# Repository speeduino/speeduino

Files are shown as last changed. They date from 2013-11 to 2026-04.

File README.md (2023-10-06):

<div align="center">

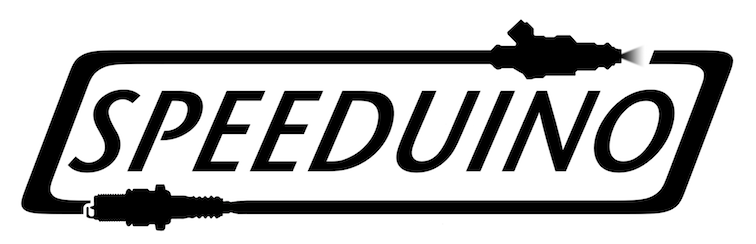
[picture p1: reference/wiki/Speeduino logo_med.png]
Speeduino











##### A low cost, DIY friendly Engine Management System (ECU) based on the Arduino framework
</div>

## Speeduino
The Speeduino project is a flexible, fully featured Engine Management Systems (EMS aka ECU) based on the low cost and open source Arduino platform. It provides the hardware, firmware and software components that make up an engine management system, all provided under open licenses. With over 1000 installations, Speeduino has matured into a product that meets the needs of the hobbyist and enthusiast community without driving prices to the levels of traditional aftermarket ECUs.

## Documentation
The Speeduino online manual can be found at: https://wiki.speeduino.com

## Where to Buy
[Pre-made Speeduino units/boards are available from a number of official resellers](https://speeduino.com/home/where-to-buy)

These resellers all contribute a portion of sales back to the project to allow for continued development to take place and we encourage sales through them whenever possible. 
 
Of course, being open source, you are free to use the design files provided here to create your own hardware! 

## Support
In addition the manual referenced above, Speeduino has a large and very vibrant community of people to help out with your setup or any questions you might add. 

* [Discord](https://discord.gg/YWCEexaNDe)
* [Speeduino Forum](https://speeduino.com/forum) 
* [Facebook](https://www.facebook.com/groups/191918764521976/)

## Contributors

This project exists thanks to all the people who contribute, both in terms of code and testing provided. If you'd like to get involved, please have a read through [Contributing](contributing.md) and then jump on Discord to discuss things further

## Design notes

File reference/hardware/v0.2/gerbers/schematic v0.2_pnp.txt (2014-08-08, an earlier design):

*Pick And Place List
*Company=
*Author=
*eMail=
*
*Project=schematic v0.2
*Date=14:46:31
*CreatedBy=Fritzing 0.9.0b.06.11.da4e
*
*
*Coordinates in mm, always center of component
*Origin 0/0=Lower left corner of PCB
*Rotation in degree (0-360, math. pos.)
*
*No;Value;Package;X;Y;Rotation;Side;Name
1;;;50.5714;-42.5374;0;Bottom;Copper Fill34
2;;;20.0533;-36.1874;0;Bottom;Copper Fill166
3;;;11.1633;-92.677;0;Bottom;Copper Fill240
4;;;51.8668;-85.0824;0;Bottom;Copper Fill12
5;;;87.8586;-102.697;0;Bottom;Copper Fill150
6;470;THT;63.2996;-22.6427;-90;Bottom;R6
7;;;50.292;-78.961;0;Bottom;Copper Fill215
8;;;54.0258;-131.907;0;Bottom;Copper Fill83
9;;;65.2082;-99.9245;0;Bottom;TXT4
10;;;73.3933;-33.6474;0;Bottom;Copper Fill142
11;;;23.3426;-89.9973;0;Bottom;Copper Fill40
12;;;19.2786;-35.3873;0;Bottom;Copper Fill343
13;;;29.4386;-32.8473;0;Bottom;Copper Fill134
14;;;56.7817;-7.3584;0;Bottom;Copper Fill328
15;680;THT;21.3896;-117.893;-90;Bottom;R18
16;;;73.3933;-26.9926;0;Bottom;Copper Fill364
17;;;88.2396;-54.6278;0;Bottom;Copper Fill210
18;;;79.9846;-80.2818;0;Bottom;Copper Fill198
19;;;49.3013;-105;0;Bottom;TXT1
20;;;24.3586;-102.697;0;Bottom;Copper Fill130
21;;;30.2133;-103.497;0;Bottom;Copper Fill55
22;0.1µF;200 mil [THT, multilayer];30.2796;-105.193;-90;Bottom;C15
23;;;96.2533;-122.192;0;Bottom;Copper Fill274
24;;;75.5142;-123.017;0;Bottom;Copper Fill93
25;;;56.7817;-9.6698;0;Bottom;Copper Fill141
26;;;74.6633;-75.5574;0;Bottom;Copper Fill105
27;;;70.8418;-103.765;0;Bottom;TXT4
28;;;92.9386;-49.3573;0;Bottom;Copper Fill37
29;;;25.1333;-103.497;0;Bottom;Copper Fill263
30;0.22µF;200 mil [THT, multilayer];58.2196;-35.3427;-90;Bottom;C6
31;;;23.3426;-67.1373;0;Bottom;Copper Fill305
32;0.22µF;200 mil [THT, multilayer];59.4896;-53.1227;90;Bottom;C8
33;;v18za2p;26.4696;-98.8427;0;Bottom;U2
34;;;30.2133;-32.0726;0;Bottom;Copper Fill322
35;;;9.9441;-39.6926;0;Bottom;Copper Fill153
36;;;31.4833;-26.9926;0;Bottom;Copper Fill346
37;;;25.1333;-101.923;0;Bottom;Copper Fill129
38;;;48.3362;-32.8981;0;Bottom;Copper Fill69
39;;300 mil [THT];68.3796;-36.5873;-90;Bottom;D5
40;;;77.5462;-32.8981;0;Bottom;Copper Fill363
41;;;83.0834;-102.697;0;Bottom;Copper Fill370
42;;;30.7848;-98.8873;0;Bottom;Copper Fill233
43;;;88.6333;-101.923;0;Bottom;Copper Fill149
44;;;67.4116;-73.0682;0;Bottom;Copper Fill202
45;;;44.1833;-28.5674;0;Bottom;Copper Fill258
46;;5 mm [THT];22.6595;-65.2437;0;Bottom;LED8
47;;;58.1533;-28.5674;0;Bottom;Copper Fill173
48;;;96.2533;-122.192;0;Bottom;Copper Fill75
49;680;THT;86.1596;-117.893;-90;Bottom;R9
50;;5 mm [THT];81.0795;-132.554;0;Bottom;LED1
51;;;36.7665;-9.6698;0;Bottom;Copper Fill185
52;;;95.0468;-58.2092;0;Bottom;Copper Fill214
53;;;23.3426;-67.1373;0;Bottom;Copper Fill113
54;;;43.4086;-27.7673;0;Bottom;Copper Fill71
55;;;49.2633;-33.8506;0;Bottom;Copper Fill255
56;;;77.2033;-59.0982;0;Bottom;Copper Fill247
57;;;30.7086;-27.7673;0;Bottom;Copper Fill171
58;;;56.6459;-1.0703;0;Bottom;TXT4
59;;;74.6633;-132.86;0;Bottom;Copper Fill87
60;;;74.6633;-122.192;0;Bottom;Copper Fill91
61;;;75.4634;-89.9973;0;Bottom;Copper Fill103
62;;;25.527;-22.6873;0;Bottom;Copper Fill375
63;;THT;10.2136;-77.2457;180;Bottom;J4
64;;;95.0468;-55.6692;0;Bottom;Copper Fill31
65;;;14.1986;-40.4673;0;Bottom;Copper Fill183
66;;;59.1058;-105.186;0;Bottom;Copper Fill340
67;;;75.4634;-89.9973;0;Bottom;Copper Fill298
68;;THT;91.2396;-23.9127;0;Bottom;JP4
69;;;95.0468;-63.213;0;Bottom;Copper Fill209
70;;;24.3586;-102.697;0;Bottom;Copper Fill265
71;;;90.3224;-63.3273;0;Bottom;Copper Fill59
72;;;89.4334;-102.697;0;Bottom;Copper Fill151
73;;;73.3933;-33.6474;0;Bottom;Copper Fill333
74;;;88.6333;-101.923;0;Bottom;Copper Fill355
75;;;53.0733;-63.7718;0;Bottom;Copper Fill121
76;;;74.6633;-130.98;0;Bottom;Copper Fill287
77;;;95.0468;-81.0692;0;Bottom;Copper Fill17
78;;TO220 [THT];93.7796;-133.387;0;Bottom;Q1
79;;;20.8534;-35.3873;0;Bottom;Copper Fill169
80;;;53.4162;-58.1965;0;Bottom;Copper Fill251
81;;;68.2498;-71.087;0;Bottom;Copper Fill203
82;;;73.8124;-123.017;0;Bottom;Copper Fill291
83;;;74.6633;-123.868;0;Bottom;Copper Fill289
84;;;11.1633;-92.677;0;Bottom;Copper Fill52
85;;;95.0468;-50.513;0;Bottom;Copper Fill32
86;;;53.0733;-123.868;0;Bottom;Copper Fill282
87;;;66.8234;-0.958547;0;Bottom;TXT4
88;;;95.0468;-70.9092;0;Bottom;Copper Fill22
89;;;71.7677;-9.6698;0;Bottom;Copper Fill73
90;;;58.1533;-104.259;0;Bottom;Copper Fill338
91;;;30.1117;-98.2396;0;Bottom;Copper Fill42
92;;;95.0468;-73.4492;0;Bottom;Copper Fill21
93;;THT;96.3196;-23.9127;0;Bottom;JP5
94;;;53.0733;-122.192;0;Bottom;Copper Fill85
95;;;31.4833;-132.86;0;Bottom;Copper Fill293
96;;THT;53.1396;-101.383;180;Bottom;JP1
97;;;31.4833;-123.868;0;Bottom;Copper Fill267
98;;DIP (Dual Inline) [THT];83.6196;-53.1227;-90;Bottom;IC3
99;;;52.2224;-64.5973;0;Bottom;Copper Fill313
100;;;52.2224;-64.5973;0;Bottom;Copper Fill122
101;;;21.844;-67.1373;0;Bottom;Copper Fill304
102;;;95.0468;-73.4492;0;Bottom;Copper Fill201
103;;;10.7188;-40.4673;0;Bottom;Copper Fill155
104;;;95.0468;-50.513;0;Bottom;Copper Fill218
105;;;74.1934;-27.7673;0;Bottom;Copper Fill366
106;;;58.1533;-104.259;0;Bottom;Copper Fill160
107;;;90.3224;-78.5673;0;Bottom;Copper Fill117
108;;;71.5782;-0.958547;0;Bottom;TXT4
109;;;9.9441;-39.6926;0;Bottom;Copper Fill359
110;;;67.4116;-83.2282;0;Bottom;Copper Fill196
111;;TO220 [THT];29.0096;-133.387;0;Bottom;Q4
112;150;THT;25.1996;-58.2027;180;Bottom;R53
113;;5 mm [THT];22.6595;-80.4837;0;Bottom;LED6
114;;;31.4833;-122.192;0;Bottom;Copper Fill98
115;;;42.545;-55.7073;0;Bottom;Copper Fill235
116;;;14.4752;-30.3567;0;Bottom;Hole1
117;;;62.0517;-1.05281;0;Bottom;TXT4
118;470;THT;69.6496;-53.1227;0;Bottom;R8
119;;;90.3224;-63.3273;0;Bottom;Copper Fill246
120;100k;THT;48.0596;-68.3627;180;Bottom;R48
121;;;31.922;-0.864567;0;Bottom;TXT4
122;10µF;200 mil [THT, tantalum];25.1996;-105.193;-90;Bottom;C16
123;;;92.7862;-102.697;0;Bottom;Copper Fill335
124;;;2.15138;-84.7786;0;Bottom;TXT4
125;;;35.7632;-58.1838;0;Bottom;Copper Fill212
126;;THT;93.7796;-32.8027;-90;Bottom;JP3
127;;;23.3426;-82.3773;0;Bottom;Copper Fill239
128;;;53.9242;-123.017;0;Bottom;Copper Fill86
129;;;34.3662;-32.8473;0;Bottom;Copper Fill253
130;;;26.1493;-91.788;0;Bottom;Copper Fill36
131;;;21.844;-89.9973;0;Bottom;Copper Fill228
132;;;95.0468;-68.3692;0;Bottom;Copper Fill24
133;;;73.8124;-123.017;0;Bottom;Copper Fill92
134;1k;THT;86.1596;-67.0927;180;Bottom;R29
135;;;77.5716;-68.4073;0;Bottom;Copper Fill104
136;;;95.0468;-88.6892;0;Bottom;Copper Fill192
137;;;83.0834;-102.697;0;Bottom;Copper Fill178
138;;;50.6418;-68.3627;0;Bottom;Arduino Mega 2560
139;1k;THT;48.0596;-75.9827;90;Bottom;R50
140;;;2.15138;-79.8868;0;Bottom;TXT4
141;;;57.6834;-58.2473;0;Bottom;Copper Fill320
142;;;77.5716;-83.6473;0;Bottom;Copper Fill295
143;;;40.7416;-55.7073;0;Bottom;Copper Fill46
144;100k;THT;31.5496;-117.893;-90;Bottom;R20
145;;;30.7086;-27.7673;0;Bottom;Copper Fill347
146;;;91.1733;-62.5018;0;Bottom;Copper Fill58
147;0.1µF;200 mil [THT, multilayer];88.6996;-100.113;90;Bottom;C13
148;;;53.0733;-132.86;0;Bottom;Copper Fill81
149;;;53.0733;-132.86;0;Bottom;Copper Fill280
150;;;96.2533;-123.868;0;Bottom;Copper Fill273
151;;;12.319;-93.8073;0;Bottom;Copper Fill242
152;;;71.7677;-9.6698;0;Bottom;Copper Fill271
153;;;36.7665;-7.3584;0;Bottom;Copper Fill378
154;;;90.3224;-78.5673;0;Bottom;Copper Fill309
155;;;52.2224;-123.017;0;Bottom;Copper Fill284
156;;;31.4833;-28.5674;0;Bottom;Copper Fill345
157;;;10.7188;-40.4673;0;Bottom;Copper Fill361
158;;;9.9441;-41.2674;0;Bottom;Copper Fill152
159;;;90.6018;-46.1442;0;Bottom;Copper Fill219
160;;;54.3052;-99.8144;0;Bottom;Copper Fill188
161;150;THT;63.2996;-72.1727;180;Bottom;R32
162;;;44.9834;-32.8473;0;Bottom;Copper Fill48
163;;;32.2834;-27.7673;0;Bottom;Copper Fill172
164;;;51.7975;-0.864567;0;Bottom;TXT4
165;;;30.6324;-123.017;0;Bottom;Copper Fill269
166;470;THT;35.3596;-25.1827;-90;Bottom;R2
167;;;22.5933;-67.8866;0;Bottom;Copper Fill111
168;;;73.8886;-89.9973;0;Bottom;Copper Fill297
169;;;58.6486;-55.7073;0;Bottom;Copper Fill139
170;;;96.2533;-130.98;0;Bottom;Copper Fill278
171;;;15.7734;-40.4673;0;Bottom;Copper Fill184
172;;TO220 [THT];72.1896;-133.387;0;Bottom;Q3
173;;300 mil [THT];40.4396;-36.5873;-90;Bottom;D1
174;;;43.4086;-27.7673;0;Bottom;Copper Fill260
175;;;30.1117;-99.5604;0;Bottom;Copper Fill230
176;;;59.1058;-105.186;0;Bottom;Copper Fill162
177;;;22.5933;-75.5066;0;Bottom;Copper Fill109
178;;;62.3062;-32.8473;0;Bottom;Copper Fill350
179;;;95.0468;-70.9092;0;Bottom;Copper Fill204
180;;;31.0134;-102.697;0;Bottom;Copper Fill57
181;1µF;200 mil [THT, multilayer];72.1896;-89.9527;180;Bottom;C11
182;;;95.0468;-81.0692;0;Bottom;Copper Fill197
183;;;58.1533;-33.6474;0;Bottom;Copper Fill135
184;;;95.0468;-86.1492;0;Bottom;Copper Fill15
185;;;95.0468;-63.213;0;Bottom;Copper Fill26
186;;;76.3524;-58.2473;0;Bottom;Copper Fill62
187;;;49.3268;-91.4324;0;Bottom;Copper Fill11
188;;;31.5468;-70.2234;0;Bottom;Copper Fill19
189;;;92.7862;-102.697;0;Bottom;Copper Fill144
190;;300 mil [THT];58.2196;-101.357;-90;Bottom;D16
191;;;42.9133;-43.528;0;Bottom;Copper Fill227
192;;;96.2533;-130.98;0;Bottom;Copper Fill79
193;;;36.7704;-0.976324;0;Bottom;TXT4
194;;;44.1833;-32.0726;0;Bottom;Copper Fill237
195;;;93.8276;-46.7538;0;Bottom;Copper Fill220
196;;;25.527;-22.6873;0;Bottom;Copper Fill186
197;;;56.7817;-9.6698;0;Bottom;Copper Fill327
198;100k;THT;74.7296;-117.893;-90;Bottom;R14
199;;;95.0468;-68.3692;0;Bottom;Copper Fill205
200;750;THT;25.1996;-34.0727;-90;Bottom;R41
201;;;95.0468;-65.9054;0;Bottom;Copper Fill207
202;;;90.3224;-89.9973;0;Bottom;Copper Fill115
203;;;59.4233;-56.5074;0;Bottom;Copper Fill137
204;;;65.6644;-101.43;0;Bottom;TXT4
205;100k;THT;86.1596;-63.2827;180;Bottom;R38
206;;;27.305;-22.6873;0;Bottom;Copper Fill376
207;;;59.4233;-54.9326;0;Bottom;Copper Fill330
208;;;30.7848;-98.8873;0;Bottom;Copper Fill44
209;;;58.9534;-27.7673;0;Bottom;Copper Fill352
210;;;27.5844;-126.942;0;Bottom;Copper Fill5
211;;;4.87971;-4.86262;0;Bottom;Hole5
212;;;76.8464;-0.958544;0;Bottom;TXT4
213;;;58.1533;-106.139;0;Bottom;Copper Fill337
214;0.1µF;200 mil [THT, multilayer];44.2496;-25.1827;90;Bottom;C3
215;;;23.3426;-74.7573;0;Bottom;Copper Fill262
216;;;49.2633;-33.8506;0;Bottom;Copper Fill68
217;0.1µF;200 mil [THT, multilayer];31.5496;-25.1827;90;Bottom;C1
218;;;71.4571;-105.25;0;Bottom;TXT3
219;;;49.9872;-69.0804;0;Bottom;Copper Fill33
220;;;88.6333;-103.497;0;Bottom;Copper Fill148
221;;;23.0886;-54.4373;0;Bottom;Copper Fill317
222;0.1µF;200 mil [THT, multilayer];59.4896;-58.2027;0;Bottom;C7
223;;;95.0468;-86.1492;0;Bottom;Copper Fill193
224;;300 mil [THT];54.4096;-54.3673;-90;Bottom;D8
225;;;73.3933;-32.0726;0;Bottom;Copper Fill143
226;;;61.9252;-128.669;0;Bottom;Copper Fill3
227;;;84.8233;-57.8282;0;Bottom;Copper Fill45
228;;;63.2333;-33.7998;0;Bottom;Copper Fill156
229;;DIP (Dual Inline) [THT];37.8996;-54.3927;180;Bottom;IC5
230;;;2.15138;-110.461;0;Bottom;TXT4
231;;TO220 [THT];50.5996;-133.387;0;Bottom;Q2
232;;300 mil [THT];17.5796;-103.948;90;Bottom;D15
233;;THT;10.2136;-117.886;180;Bottom;J2
234;;;52.2224;-68.4073;0;Bottom;Copper Fill311
235;;;74.6633;-132.86;0;Bottom;Copper Fill286
236;;;30.2133;-33.6474;0;Bottom;Copper Fill132
237;;;63.2333;-31.9202;0;Bottom;Copper Fill157
238;;;31.0134;-32.8473;0;Bottom;Copper Fill324
239;;;46.8981;-101.29;0;Bottom;TXT2
240;;;46.7741;-7.3584;0;Bottom;Copper Fill354
241;;5 mm [THT];37.8995;-132.554;0;Bottom;LED3
242;;;9.144;-40.4673;0;Bottom;Copper Fill154
243;;;23.8633;-55.2374;0;Bottom;Copper Fill315
244;;;90.3224;-74.7573;0;Bottom;Copper Fill116
245;;;82.2833;-101.923;0;Bottom;Copper Fill368
246;;;60.2234;-55.7073;0;Bottom;Copper Fill332
247;;;79.8097;-116.623;0;Bottom;Hole3
248;;;56.8833;-57.4726;0;Bottom;Copper Fill319
249;;;25.1333;-101.923;0;Bottom;Copper Fill264
250;;;35.2933;-33.7998;0;Bottom;Copper Fill66
251;;;79.9846;-65.0418;0;Bottom;Copper Fill208
252;;;14.9733;-39.6926;0;Bottom;Copper Fill372
253;;;95.4024;-123.017;0;Bottom;Copper Fill275
254;;;95.0468;-91.2292;0;Bottom;Copper Fill190
255;150;THT;63.2996;-82.3327;0;Bottom;R27
256;;;29.4386;-102.697;0;Bottom;Copper Fill244
257;;;23.8633;-53.6626;0;Bottom;Copper Fill125
258;;;74.6633;-75.5574;0;Bottom;Copper Fill300
259;;300 mil [THT];42.9796;-129.348;90;Bottom;D11
260;;;95.0468;-83.6092;0;Bottom;Copper Fill16
261;;;95.0468;-78.5292;0;Bottom;Copper Fill199
262;;;72.6186;-27.7673;0;Bottom;Copper Fill365
263;;;39.8018;-103.548;0;Bottom;Copper Fill7
264;;;57.2262;-105.186;0;Bottom;Copper Fill339
265;680;THT;32.8196;-67.0927;0;Bottom;R34
266;;;44.1833;-26.9926;0;Bottom;Copper Fill70
267;;;96.2533;-123.868;0;Bottom;Copper Fill74
268;;5 mm [THT];22.6595;-72.8637;0;Bottom;LED7
269;;;2.16718;-125.423;0;Bottom;TXT4
270;;;79.4258;-32.8981;0;Bottom;Copper Fill165
271;;;35.2933;-33.7998;0;Bottom;Copper Fill252
272;;;95.0468;-94.0232;0;Bottom;Copper Fill189
273;;;78.4733;-33.8506;0;Bottom;Copper Fill163
274;;;54.3433;-57.2694;0;Bottom;Copper Fill250
275;;;28.3718;-67.0992;0;Bottom;Copper Fill206
276;1µF;200 mil [THT, multilayer];9.95962;-37.8827;90;Bottom;C20
277;;;78.4733;-31.971;0;Bottom;Copper Fill164
278;;;97.2058;-131.907;0;Bottom;Copper Fill279
279;;;10.0076;-93.8073;0;Bottom;Copper Fill241
280;;;53.0733;-123.868;0;Bottom;Copper Fill84
281;100k;THT;48.0596;-64.5527;180;Bottom;R49
282;;;21.844;-74.7573;0;Bottom;Copper Fill110
283;;;74.6633;-130.98;0;Bottom;Copper Fill88
284;;;44.1833;-33.6474;0;Bottom;Copper Fill47
285;;;75.6158;-131.907;0;Bottom;Copper Fill288
286;;;49.9872;-69.0804;0;Bottom;Copper Fill222
287;;;19.2786;-35.3873;0;Bottom;Copper Fill168
288;;;9.9441;-41.2674;0;Bottom;Copper Fill358
289;;;84.8614;-76.0908;0;Bottom;Copper Fill191
290;;;32.4358;-131.907;0;Bottom;Copper Fill96
291;;;77.5716;-83.6473;0;Bottom;Copper Fill100
292;;;97.2058;-131.907;0;Bottom;Copper Fill80
293;100k;THT;96.3196;-117.893;-90;Bottom;R11
294;1k;THT;26.4696;-117.893;-90;Bottom;R19
295;;;73.8886;-74.7573;0;Bottom;Copper Fill302
296;;;2.52775;-60.4134;0;Bottom;TXT4
297;;;53.0733;-69.2582;0;Bottom;Copper Fill118
298;680;THT;32.8196;-87.4127;0;Bottom;R28
299;;;91.1733;-90.8482;0;Bottom;Copper Fill306
300;470;THT;78.5396;-22.6427;-90;Bottom;R22
301;;;82.2833;-103.497;0;Bottom;Copper Fill367
302;;;32.4358;-131.907;0;Bottom;Copper Fill294
303;;;57.6834;-58.2473;0;Bottom;Copper Fill147
304;;300 mil [THT];49.3296;-36.6381;90;Bottom;D4
305;;;87.8586;-102.697;0;Bottom;Copper Fill356
306;;;96.884;-0.864614;0;Bottom;TXT4
307;2.49k;THT;40.4396;-25.1827;90;Bottom;R1
308;;;74.6633;-123.868;0;Bottom;Copper Fill90
309;;300 mil [THT];86.1596;-129.348;90;Bottom;D9
310;;;91.9923;-0.864614;0;Bottom;TXT4
311;;;59.4233;-54.9326;0;Bottom;Copper Fill138
312;;;23.3426;-82.3773;0;Bottom;Copper Fill51
313;;;24.6634;-54.4373;0;Bottom;Copper Fill127
314;;;90.3224;-74.7573;0;Bottom;Copper Fill308
315;;300 mil [THT];49.3296;-54.4181;90;Bottom;D7
316;;;73.8886;-89.9973;0;Bottom;Copper Fill102
317;;;9.144;-40.4673;0;Bottom;Copper Fill360
318;;;82.2833;-101.923;0;Bottom;Copper Fill176
319;;THT;93.7796;-37.8827;90;Bottom;JP2
320;;;95.0468;-91.2292;0;Bottom;Copper Fill13
321;;;44.1833;-33.6474;0;Bottom;Copper Fill236
322;;;58.1533;-26.9926;0;Bottom;Copper Fill174
323;;;30.2133;-32.0726;0;Bottom;Copper Fill133
324;;;2.38265;-98.9839;0;Bottom;TXT4
325;;;54.3433;-59.149;0;Bottom;Copper Fill63
326;;THT;64.4426;-7.42867;90;Bottom;J1
327;;;56.8833;-57.4726;0;Bottom;Copper Fill146
328;;;26.1493;-93.312;0;Bottom;Copper Fill223
329;;;86.818;-0.864614;0;Bottom;TXT4
330;;THT;10.2136;-53.0357;180;Bottom;J5
331;;;20.8534;-35.3873;0;Bottom;Copper Fill344
332;;;63.2333;-33.7998;0;Bottom;Copper Fill349
333;;;59.4233;-56.5074;0;Bottom;Copper Fill329
334;;;95.0468;-58.2092;0;Bottom;Copper Fill30
335;;;25.9334;-102.697;0;Bottom;Copper Fill131
336;;;46.4859;-0.976324;0;Bottom;TXT4
337;;;30.1117;-99.5604;0;Bottom;Copper Fill41
338;;;23.3426;-89.9973;0;Bottom;Copper Fill229
339;0.3µF;200 mil [THT, multilayer];20.1196;-37.8827;90;Bottom;C18
340;;;31.4833;-130.98;0;Bottom;Copper Fill95
341;;;95.0468;-75.9892;0;Bottom;Copper Fill200
342;100k;THT;53.1396;-117.893;-90;Bottom;R17
343;;;49.4801;-97.2903;0;Bottom;TXT1
344;;;54.3433;-57.2694;0;Bottom;Copper Fill64
345;;;31.4833;-26.9926;0;Bottom;Copper Fill170
346;1k;THT;48.0596;-117.893;-90;Bottom;R16
347;;;95.0468;-78.5292;0;Bottom;Copper Fill18
348;;;29.4386;-102.697;0;Bottom;Copper Fill56
349;;;14.9733;-39.6926;0;Bottom;Copper Fill182
350;;;55.8546;-59.3014;0;Bottom;Copper Fill213
351;;;95.0468;-60.7492;0;Bottom;Copper Fill28
352;;;2.15138;-120.433;0;Bottom;TXT4
353;;;77.2033;-57.4218;0;Bottom;Copper Fill248
354;;;77.2033;-57.4218;0;Bottom;Copper Fill61
355;;300 mil [THT];64.5696;-129.348;90;Bottom;D10
356;;;18.7452;-128.669;0;Bottom;Copper Fill1
357;;;74.6633;-122.192;0;Bottom;Copper Fill290
358;;;20.0533;-34.6126;0;Bottom;Copper Fill342
359;;;53.9242;-68.4073;0;Bottom;Copper Fill120
360;;5 mm [THT];16.3098;-132.554;0;Bottom;LED4
361;2.49k;THT;54.4096;-23.9127;90;Bottom;R3
362;;;73.3933;-26.9926;0;Bottom;Copper Fill180
363;;;82.0115;-0.914567;0;Bottom;TXT4
364;;;15.7734;-40.4673;0;Bottom;Copper Fill374
365;;;42.9768;-57.5996;0;Bottom;Copper Fill29
366;;;82.2833;-103.497;0;Bottom;Copper Fill175
367;;;74.6633;-89.2226;0;Bottom;Copper Fill101
368;470;THT;49.3296;-22.6427;-90;Bottom;R4
369;;;50.2158;-32.8981;0;Bottom;Copper Fill257
370;;;4.87971;-133.133;0;Bottom;Hole4
371;;;53.0733;-69.2582;0;Bottom;Copper Fill310
372;;;53.9242;-123.017;0;Bottom;Copper Fill285
373;;300 mil [THT];21.3896;-129.348;90;Bottom;D12
374;;;21.844;-89.9973;0;Bottom;Copper Fill39
375;1k;THT;45.5196;-75.9827;90;Bottom;R51
376;;;27.305;-22.6873;0;Bottom;Copper Fill187
377;;;77.2033;-59.0982;0;Bottom;Copper Fill60
378;100k;THT;86.1596;-78.5227;180;Bottom;R37
379;;;14.5223;-7.21443;0;Bottom;Hole2
380;;;30.2133;-33.6474;0;Bottom;Copper Fill321
381;;;2.15138;-74.8068;0;Bottom;TXT4
382;;;25.9334;-102.697;0;Bottom;Copper Fill266
383;;;46.7741;-9.6698;0;Bottom;Copper Fill159
384;680;THT;32.8196;-82.3327;0;Bottom;R26
385;;;32.3342;-123.017;0;Bottom;Copper Fill270
386;;;21.844;-74.7573;0;Bottom;Copper Fill261
387;1µF;200 mil [THT, multilayer];72.1896;-74.7127;180;Bottom;C12
388;1µF;200 mil [THT, multilayer];26.4696;-54.3927;0;Bottom;C22
389;;;77.5716;-68.4073;0;Bottom;Copper Fill299
390;;;53.0733;-130.98;0;Bottom;Copper Fill82
391;;300 mil [THT];35.3596;-36.5873;90;Bottom;D2
392;;;58.1533;-26.9926;0;Bottom;Copper Fill351
393;;;2.52775;-55.6157;0;Bottom;TXT4
394;;;94.6658;-102.697;0;Bottom;Copper Fill145
395;1k;THT;72.1896;-58.2027;0;Bottom;R21
396;;;40.3352;-128.669;0;Bottom;Copper Fill2
397;;;44.2468;-66.4388;0;Bottom;Copper Fill23
398;;;95.0468;-53.2054;0;Bottom;Copper Fill217
399;;;78.4733;-33.8506;0;Bottom;Copper Fill362
400;;;44.1833;-26.9926;0;Bottom;Copper Fill259
401;;;94.6658;-102.697;0;Bottom;Copper Fill336
402;;;31.4833;-132.86;0;Bottom;Copper Fill94
403;;;23.0886;-54.4373;0;Bottom;Copper Fill126
404;0.22µF;200 mil [THT, multilayer];73.4596;-35.3427;-90;Bottom;C10
405;;;21.844;-82.3773;0;Bottom;Copper Fill50
406;;;96.2533;-48.608;0;Bottom;Copper Fill38
407;;;30.2133;-103.497;0;Bottom;Copper Fill243
408;150;THT;25.1996;-50.5827;0;Bottom;R52
409;;;64.1858;-32.8473;0;Bottom;Copper Fill158
410;1k;THT;86.1596;-86.1427;180;Bottom;R24
411;;;46.7868;-86.9874;0;Bottom;Copper Fill10
412;;;14.9733;-41.2674;0;Bottom;Copper Fill181
413;;;29.4386;-98.8873;0;Bottom;Copper Fill232
414;;;36.2458;-32.8473;0;Bottom;Copper Fill254
415;10k;THT;83.6196;-22.6427;90;Bottom;R40
416;;;76.3524;-58.2473;0;Bottom;Copper Fill249
417;;;58.9534;-32.8473;0;Bottom;Copper Fill326
418;;THT;26.4696;-18.8327;0;Bottom;MPX4250A
419;680;THT;32.8196;-74.7127;0;Bottom;R33
420;;;12.5222;-61.8668;0;Bottom;Copper Fill27
421;;;44.9834;-27.7673;0;Bottom;Copper Fill72
422;;;20.0533;-34.6126;0;Bottom;Copper Fill167
423;;;2.5365;-45.5201;0;Bottom;TXT4
424;;;30.1117;-98.2396;0;Bottom;Copper Fill231
425;;;95.4024;-123.017;0;Bottom;Copper Fill76
426;;;29.4386;-32.8473;0;Bottom;Copper Fill323
427;;;41.6375;-0.864567;0;Bottom;TXT4
428;1k;THT;91.2396;-117.893;-90;Bottom;R10
429;;;91.1733;-90.8482;0;Bottom;Copper Fill114
430;;;96.448;-35.9101;0;Bottom;TXT4
431;;;25.1333;-103.497;0;Bottom;Copper Fill128
432;;;96.2533;-132.86;0;Bottom;Copper Fill277
433;;;21.844;-67.1373;0;Bottom;Copper Fill112
434;;;74.6633;-73.9826;0;Bottom;Copper Fill301
435;;5 mm [THT];59.4895;-132.554;0;Bottom;LED2
436;;THT;10.2136;-96.1358;180;Bottom;J3
437;;;36.7665;-9.6698;0;Bottom;Copper Fill377
438;47µF;200 mil [THT, tantalum];82.3496;-100.113;90;Bottom;C14
439;;;53.9242;-68.4073;0;Bottom;Copper Fill312
440;;DIP (Dual Inline) [THT];74.7296;-67.0927;180;Bottom;IC2
441;;;37.8714;-100.526;0;Bottom;Copper Fill8
442;680;THT;42.9796;-117.893;-90;Bottom;R15
443;150;THT;56.9496;-87.4127;180;Bottom;R25
444;;;2.47691;-93.7157;0;Bottom;TXT4
445;;;58.6486;-55.7073;0;Bottom;Copper Fill331
446;10k;THT;86.1596;-22.6427;90;Bottom;R39
447;;;96.2533;-132.86;0;Bottom;Copper Fill78
448;;;90.3224;-89.9973;0;Bottom;Copper Fill307
449;;;20.0533;-36.1874;0;Bottom;Copper Fill341
450;;;2.15138;-69.9149;0;Bottom;TXT4
451;;;23.8633;-53.6626;0;Bottom;Copper Fill316
452;;;95.0468;-88.6892;0;Bottom;Copper Fill14
453;680;THT;64.5696;-117.893;-90;Bottom;R12
454;;;58.1533;-32.0726;0;Bottom;Copper Fill136
455;;;2.15138;-115.447;0;Bottom;TXT4
456;;;81.5086;-102.697;0;Bottom;Copper Fill369
457;;;12.319;-93.8073;0;Bottom;Copper Fill54
458;;;75.4634;-74.7573;0;Bottom;Copper Fill108
459;;;14.1986;-40.4673;0;Bottom;Copper Fill373
460;;;58.1533;-33.6474;0;Bottom;Copper Fill325
461;;;97.1042;-123.017;0;Bottom;Copper Fill77
462;;;14.9733;-41.2674;0;Bottom;Copper Fill371
463;;;36.2458;-32.8473;0;Bottom;Copper Fill67
464;;;95.0468;-75.9892;0;Bottom;Copper Fill20
465;;;95.0468;-55.6692;0;Bottom;Copper Fill216
466;;;49.2633;-31.971;0;Bottom;Copper Fill256
467;;;21.844;-82.3773;0;Bottom;Copper Fill238
468;;;84.8233;-56.1518;0;Bottom;Copper Fill234
469;;;74.1934;-32.8473;0;Bottom;Copper Fill334
470;3.9k;THT;62.0296;-62.0127;0;Bottom;R7
471;;;95.0468;-83.6092;0;Bottom;Copper Fill194
472;;;74.6633;-73.9826;0;Bottom;Copper Fill106
473;;;2.52775;-50.4416;0;Bottom;TXT4
474;;;40.4114;-99.8906;0;Bottom;Copper Fill9
475;;;68.3797;-23.9126;0;Bottom;Hole6
476;;;32.3342;-123.017;0;Bottom;Copper Fill99
477;;;22.5933;-83.1266;0;Bottom;Copper Fill49
478;;;49.1744;-126.84;0;Bottom;Copper Fill6
479;;;91.3337;-35.766;0;Bottom;TXT4
480;;DIP (Dual Inline) [THT];74.7296;-82.3327;180;Bottom;IC1
481;;;97.1042;-123.017;0;Bottom;Copper Fill276
482;;;31.0134;-102.697;0;Bottom;Copper Fill245
483;;;31.4833;-122.192;0;Bottom;Copper Fill268
484;;;42.9133;-45.052;0;Bottom;Copper Fill226
485;;;57.2262;-105.186;0;Bottom;Copper Fill161
486;0.01µF;200 mil [THT, multilayer];15.0396;-37.8827;90;Bottom;C19
487;;;29.4386;-98.8873;0;Bottom;Copper Fill43
488;100k;THT;86.1596;-74.7127;180;Bottom;R36
489;;;23.8633;-55.2374;0;Bottom;Copper Fill124
490;0.22µF;200 mil [THT, multilayer];30.2796;-35.3427;-90;Bottom;C2
491;;;75.6158;-131.907;0;Bottom;Copper Fill89
492;;;83.5152;-128.669;0;Bottom;Copper Fill4
493;;;32.2834;-27.7673;0;Bottom;Copper Fill348
494;;;91.2146;-30.4037;0;Bottom;TXT4
495;;;75.5142;-123.017;0;Bottom;Copper Fill292
496;1k;THT;69.6496;-117.893;-90;Bottom;R13
497;;;26.1493;-91.788;0;Bottom;Copper Fill224
498;;5 mm [THT];22.6595;-88.1037;0;Bottom;LED5
499;;;53.0733;-122.192;0;Bottom;Copper Fill283
500;;;46.7741;-9.6698;0;Bottom;Copper Fill353
501;100k;THT;86.1596;-89.9527;180;Bottom;R35
502;;;81.1022;-58.8188;0;Bottom;Copper Fill211
503;;;73.3933;-28.5674;0;Bottom;Copper Fill179
504;;;74.6633;-89.2226;0;Bottom;Copper Fill296
505;;;73.8886;-74.7573;0;Bottom;Copper Fill107
506;;300 mil [THT];83.6196;-36.5873;-90;Bottom;D14
507;;;40.3733;-45.052;0;Bottom;Copper Fill225
508;;;52.2224;-68.4073;0;Bottom;Copper Fill119
509;;;53.9242;-64.5973;0;Bottom;Copper Fill314
510;;;81.5086;-102.697;0;Bottom;Copper Fill177
511;5V;TO220 [THT];95.3036;-102.653;90;Bottom;U1
512;;300 mil [THT];78.5396;-36.6381;90;Bottom;D13
513;;300 mil [THT];54.4096;-36.5873;-90;Bottom;D3
514;;;54.0258;-131.907;0;Bottom;Copper Fill281
515;;;89.4334;-102.697;0;Bottom;Copper Fill357
516;;;31.4833;-123.868;0;Bottom;Copper Fill97
517;;;71.7677;-7.3584;0;Bottom;Copper Fill272
518;;;24.6634;-54.4373;0;Bottom;Copper Fill318
519;;;54.4322;-81.6534;0;Bottom;Copper Fill195
520;;;53.4162;-58.1965;0;Bottom;Copper Fill65
521;0.22µF;200 mil [THT, multilayer];44.2496;-35.3427;-90;Bottom;C4
522;1k;THT;86.1596;-82.3327;180;Bottom;R23
523;1k;THT;86.1596;-70.9027;180;Bottom;R30
524;;;75.4634;-74.7573;0;Bottom;Copper Fill303
525;0.1µF;200 mil [THT, multilayer];73.4596;-25.1827;90;Bottom;C9
526;;;96.375;-30.5492;0;Bottom;TXT4
527;;;26.1493;-93.312;0;Bottom;Copper Fill35
528;0.1µF;200 mil [THT, multilayer];58.2196;-25.1827;90;Bottom;C5
529;;300 mil [THT];63.2996;-36.5873;90;Bottom;D6
530;;;53.9242;-64.5973;0;Bottom;Copper Fill123
531;;;60.2234;-55.7073;0;Bottom;Copper Fill140
532;150;THT;63.2996;-67.0927;0;Bottom;R31
533;;;10.0076;-93.8073;0;Bottom;Copper Fill53
534;;;95.0468;-65.9054;0;Bottom;Copper Fill25
535;;;88.6968;-20.7188;0;Bottom;Copper Fill221

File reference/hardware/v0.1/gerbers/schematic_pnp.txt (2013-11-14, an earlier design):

*Pick And Place List
*Company=
*Author=
*eMail=
*
*Project=schematic
*Date=06:20:07
*CreatedBy=Fritzing 0.8.3b.07.27.048f
*
*
*Coordinates in mm, always center of component
*Origin 0/0=Lower left corner of PCB
*Rotation in degree (0-360, math. pos.)
*
*No;Value;Package;X;Y;Rotation;Side;Name
1;;;3.77152;-52.9077;0;Bottom;TXT3
2;;;52.5959;-14.949;0;Bottom;Via2
3;;;3.77152;-7.32882;0;Bottom;TXT3
4;;;2.7661;-32.9562;90;Bottom;TXT4
5;;300 mil [THT];66.5913;-47.9689;180;Bottom;D1
6;;;5.36398;-10.7155;0;Bottom;TXT3
7;;;3.72105;-1.96659;0;Bottom;TXT3
8;;THT;124.732;-50.6758;0;Bottom;Ignition Outputs 1/2
9;;;5.54048;-43.731;0;Bottom;TXT3
10;;;127.667;-17.3477;0;Bottom;TXT3
11;;;127.667;-27.6488;0;Bottom;TXT3
12;;TO220 [THT];25.6719;-7.32886;-90;Bottom;Q3
13;;;126.513;-47.9688;0;Bottom;TXT3
14;1k;THT;24.6559;-32.7289;90;Bottom;R9
15;;;126.936;-12.5499;0;Bottom;TXT3
16;10k;THT;70.3759;-30.1889;0;Bottom;R1
17;1k;THT;47.5159;-25.1089;90;Bottom;R6
18;;;7.40668;-26.0261;90;Bottom;TXT4
19;100nF;200 mil [THT, multilayer];60.2159;-40.3489;-90;Bottom;C1
20;1k;THT;29.7359;-40.3489;-90;Bottom;R8
21;;;125.127;-56.1533;0;Bottom;TXT3
22;;300 mil [THT];18.2805;-53.0489;0;Bottom;D3
23;;THT;5.85995;-50.3419;180;Bottom;Ignition outputs 3/4
24;;TO220 [THT];38.3719;-40.3489;-90;Bottom;Q1
25;;;57.2777;-19.8877;0;Bottom;TXT3
26;;TO220 [THT];25.6719;-20.0289;-90;Bottom;Q4
27;;;5.17265;-27.4361;90;Bottom;TXT4
28;;THT;60.2159;-22.5689;0;Bottom;J1
29;;TO220 [THT];38.3719;-27.6489;-90;Bottom;Q2
30;;THT;124.732;-4.95585;0;Bottom;Injector Outputs
31;;;57.419;-25.2499;0;Bottom;TXT3
32;;;127.667;-22.4277;0;Bottom;TXT3
33;10k;THT;70.3759;-22.5689;0;Bottom;R2
34;;THT;83.0759;-28.9189;90;Bottom;U1
35;10k;THT;47.5159;-37.8089;-90;Bottom;R3
36;;;127.717;-42.4655;0;Bottom;TXT3
37;;;126.936;-37.6677;0;Bottom;TXT3
38;10k;THT;22.1159;-32.7289;90;Bottom;R10
39;;;127.667;-32.5877;0;Bottom;TXT3
40;;THT;5.85995;-4.62191;180;Bottom;Injector outputs 3/4
41;1k;THT;50.0559;-37.8089;-90;Bottom;R4
42;;;67.8783;-28.9189;0;Bottom;Arduino Mega 2560
43;;;108.476;-37.809;0;Bottom;Via1
44;;THT;124.732;-27.7759;0;Bottom;Inputs
45;;;34.8409;-11.1487;0;Bottom;TXT2
46;;;3.77152;-47.9688;0;Bottom;TXT3
47;100nF;200 mil [THT, multilayer];19.5759;-40.3489;-90;Bottom;C3
48;;THT;37.5229;-3.77299;90;Bottom;12v Input
49;;;127.385;-6.90548;0;Bottom;TXT3
50;;;126.538;-52.9077;0;Bottom;TXT3
51;10k;THT;44.9759;-25.1089;90;Bottom;R5
52;;;127.385;-2.38993;0;Bottom;TXT3
53;;;40.2294;-11.171;0;Bottom;TXT2
54;100nF;200 mil [THT, multilayer];70.3759;-35.2689;0;Bottom;C2
55;;300 mil [THT];69.1313;-40.3489;180;Bottom;D2
56;100nF;200 mil [THT, multilayer];14.4959;-40.3489;-90;Bottom;C4
57;10k;THT;27.1959;-40.3489;-90;Bottom;R7
58;;;126.35;-8.92811;0;Bottom;TXT3
59;;300 mil [THT];18.2805;-47.9689;0;Bottom;D4

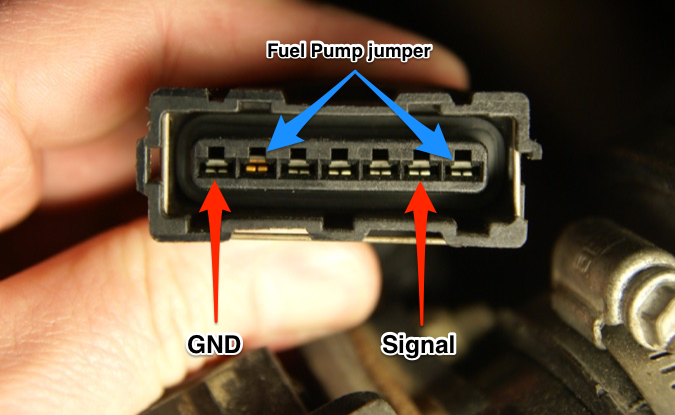
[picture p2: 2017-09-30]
reference/wiki/MX5/AFM_fuel_pump.png

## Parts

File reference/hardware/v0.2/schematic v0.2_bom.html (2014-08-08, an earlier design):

Label | Part Type | Properties
Arduino Mega 2560 | Arduino Mega 2560 (Rev3) | type Arduino MEGA 2560 (Rev3); part # Arduino Mega 2560
C1 | Ceramic Capacitor | voltage 6.3V; package 200 mil [THT, multilayer]; capacitance 0.1µF
C2 | Ceramic Capacitor | voltage 6.3V; package 200 mil [THT, multilayer]; capacitance 0.22µF
C3 | Ceramic Capacitor | voltage 6.3V; package 200 mil [THT, multilayer]; capacitance 0.1µF
C4 | Ceramic Capacitor | voltage 6.3V; package 200 mil [THT, multilayer]; capacitance 0.22µF
C5 | Ceramic Capacitor | voltage 6.3V; package 200 mil [THT, multilayer]; capacitance 0.1µF
C6 | Ceramic Capacitor | voltage 6.3V; package 200 mil [THT, multilayer]; capacitance 0.22µF
C7 | Ceramic Capacitor | voltage 6.3V; package 200 mil [THT, multilayer]; capacitance 0.1µF
C8 | Ceramic Capacitor | voltage 6.3V; package 200 mil [THT, multilayer]; capacitance 0.22µF
C9 | Ceramic Capacitor | voltage 6.3V; package 200 mil [THT, multilayer]; capacitance 0.1µF
C10 | Ceramic Capacitor | voltage 6.3V; package 200 mil [THT, multilayer]; capacitance 0.22µF
C11 | Ceramic Capacitor | voltage 6.3V; package 200 mil [THT, multilayer]; capacitance 1µF
C12 | Ceramic Capacitor | voltage 6.3V; package 200 mil [THT, multilayer]; capacitance 1µF
C13 | Ceramic Capacitor | voltage 50V; package 200 mil [THT, multilayer]; capacitance 0.1µF
C14 | Tantalum Capacitor | voltage 10V; package 200 mil [THT, tantalum]; capacitance 47µF
C15 | Ceramic Capacitor | voltage 50V; package 200 mil [THT, multilayer]; capacitance 0.1µF
C16 | Tantalum Capacitor | voltage 35V; package 200 mil [THT, tantalum]; capacitance 10µF
C18 | Ceramic Capacitor | voltage 6.3V; package 200 mil [THT, multilayer]; capacitance 0.3µF
C19 | Ceramic Capacitor | voltage 6.3V; package 200 mil [THT, multilayer]; capacitance 0.01µF
C20 | Ceramic Capacitor | voltage 6.3V; package 200 mil [THT, multilayer]; capacitance 1µF
C22 | Ceramic Capacitor | voltage 6.3V; package 200 mil [THT, multilayer]; capacitance 1µF
D1 | Schottky Diode | package 300 mil [THT]; type Schottky; part # 1N5818
D2 | Schottky Diode | package 300 mil [THT]; type Schottky; part # 1N5818
D3 | Schottky Diode | package 300 mil [THT]; type Schottky; part # 1N5818
D4 | Schottky Diode | package 300 mil [THT]; type Schottky; part # 1N5818
D5 | Schottky Diode | package 300 mil [THT]; type Schottky; part # 1N5818
D6 | Schottky Diode | package 300 mil [THT]; type Schottky; part # 1N5818
D7 | Schottky Diode | package 300 mil [THT]; type Schottky; part # 1N5818
D8 | Schottky Diode | package 300 mil [THT]; type Schottky; part # 1N5818
D9 | Rectifier Diode | package 300 mil [THT]; type Rectifier; part # 1N4004
D10 | Rectifier Diode | package 300 mil [THT]; type Rectifier; part # 1N4004
D11 | Rectifier Diode | package 300 mil [THT]; type Rectifier; part # 1N4004
D12 | Rectifier Diode | package 300 mil [THT]; type Rectifier; part # 1N4004
D13 | Schottky Diode | package 300 mil [THT]; type Schottky; part # 1N5818
D14 | Schottky Diode | package 300 mil [THT]; type Schottky; part # 1N5818
D15 | Schottky Diode | package 300 mil [THT]; type Schottky; part # 1N5818
D16 | Zener Diode | power dissipation 0.5W; package 300 mil [THT]; type Zener; breakdown voltage 5.1V; part # 1N5919BG
IC1 | IC | chip label IC; true; package DIP (Dual Inline) [THT]; pin spacing 300mil; pins 8; hole size 1.0mm,0.508mm; part # TC4424EPA
IC2 | IC | chip label IC; true; package DIP (Dual Inline) [THT]; pin spacing 300mil; pins 8; hole size 1.0mm,0.508mm; part # TC4424EPA
IC3 | Dual VR Conditioner | chip label Dual VR Conditioner; true; package DIP (Dual Inline) [THT]; pin spacing 300mil; pins 8; hole size 1.0mm,0.508mm
IC5 | IC | chip label IC; true; package DIP (Dual Inline) [THT]; pin spacing 300mil; pins 8; hole size 1.0mm,0.508mm; part # TC4425EPA
J1 | Screw terminal - 14 pins | package THT; pin spacing 0.197in (5.0mm); pins 14; hole size 1.5mm,0.508mm
J2 | Screw terminal - 4 pins | package THT; pin spacing 0.197in (5.0mm); pins 4; hole size 1.5mm,0.508mm
J3 | Screw terminal - 2 pins | package THT; pin spacing 0.197in (5.0mm); pins 2; hole size 1.5mm,0.508mm
J4 | Screw terminal - 4 pins | package THT; pin spacing 0.197in (5.0mm); pins 4; hole size 1.5mm,0.508mm
J5 | Screw terminal - 4 pins | package THT; pin spacing 0.197in (5.0mm); pins 4; hole size 1.5mm,0.508mm
JP1 | Generic female header - 3 pins | package THT; pin spacing 0.1in (2.54mm); row single; pins 3; form ♀ (female); hole size 1.0mm,0.508mm
JP2 | Generic female header - 3 pins | package THT; pin spacing 0.1in (2.54mm); row single; pins 3; form ♀ (female); hole size 1.0mm,0.508mm
JP3 | Generic female header - 3 pins | package THT; pin spacing 0.1in (2.54mm); row single; pins 3; form ♀ (female); hole size 1.0mm,0.508mm
JP4 | Generic female header - 2 pins | package THT; pin spacing 0.1in (2.54mm); row single; pins 2; form ♀ (female); hole size 1.0mm,0.508mm
JP5 | Generic female header - 2 pins | package THT; pin spacing 0.1in (2.54mm); row single; pins 2; form ♀ (female); hole size 1.0mm,0.508mm
LED1 | Red (633nm) LED | leg yes; package 5 mm [THT]; color Red (633nm)
LED2 | Red (633nm) LED | leg yes; package 5 mm [THT]; color Red (633nm)
LED3 | Red (633nm) LED | leg yes; package 5 mm [THT]; color Red (633nm)
LED4 | Red (633nm) LED | leg yes; package 5 mm [THT]; color Red (633nm)
LED5 | Red (633nm) LED | leg yes; package 5 mm [THT]; color Red (633nm)
LED6 | Red (633nm) LED | leg yes; package 5 mm [THT]; color Red (633nm)
LED7 | Red (633nm) LED | leg yes; package 5 mm [THT]; color Red (633nm)
LED8 | Red (633nm) LED | leg yes; package 5 mm [THT]; color Red (633nm)
MPX4250A | Generic female header - 6 pins | package THT; pin spacing 0.1in (2.54mm); row single; pins 6; form ♀ (female); hole size 1.0mm,0.508mm
Part2 | Schematic Frame | descr Inlet Air Temperature sensor; sheet 1/1; date 1404042789; filename Untitled Sketch 4.fzz
Part3 | Schematic Frame | descr Coolant Temperature Sensor; sheet 1/1; date 1404042789; filename Untitled Sketch 4.fzz
Part4 | Schematic Frame | descr Throttle Position Sensor; sheet 1/1; date 1404042789; filename Untitled Sketch 6.fzz; project Speeduino v0.2
Part5 | Schematic Frame | descr Battery Reference Voltage; sheet 1/1; date 1404042789; filename Untitled Sketch 4.fzz
Part6 | Schematic Frame | descr Injector 1; sheet 1/1; date 1404088041; filename schematic v0.2.fzz
Part7 | Schematic Frame | descr Sensor Screw connector 1; sheet 1/1; date 1404088363; filename schematic v0.2.fzz; project Speeduino v0.2
Part8 | Schematic Frame | descr Injector 3; sheet 1/1; date 1404088041; filename schematic v0.2.fzz
Part9 | Schematic Frame | descr Injector 2; sheet 1/1; date 1404088041; filename schematic v0.2.fzz
Part10 | Schematic Frame | descr Injector 4; sheet 1/1; date 1404088041; filename schematic v0.2.fzz
Part11 | Schematic Frame | descr O2 Sensor; sheet 1/1; date 1404042789; filename Untitled Sketch 6.fzz; project Speeduino v0.2
Part12 | Schematic Frame | descr Ignitor output 1; sheet 1/1; date 1404274298; filename schematic v0.2.fzz
Part13 | Schematic Frame | descr Ignitor output 2; sheet 1/1; date 1404274298; filename schematic v0.2.fzz
Part14 | Schematic Frame | descr Power supply; sheet 1/1; date 1404304523; filename schematic v0.2.fzz
Part15 | Schematic Frame | descr Crank and Cam sensors; sheet 1/1; date 1404042789; filename Untitled Sketch 4.fzz
Part16 | Schematic Frame | descr MAP sensor input; sheet 1/1; date 1405641290; filename schematic v0.2.fzz; project Speeduino v0.2
Part18 | Schematic Frame | sheet 1/1; date 1405660608; filename schematic v0.2.fzz
Q1 | Basic FET N-Channel | package TO220 [THT]; type n-channel; part # VND7NV04
Q2 | Basic FET N-Channel | package TO220 [THT]; type n-channel; part # VND7NV04
Q3 | Basic FET N-Channel | package TO220 [THT]; type n-channel; part # VND7NV04
Q4 | Basic FET N-Channel | package TO220 [THT]; type n-channel; part # VND7NV04
R1 | 2.49kΩ Resistor | power 3W; bands 4; package THT; pin spacing 400 mil; tolerance ±5%; resistance 2.49kΩ
R2 | 470Ω Resistor | power 3W; bands 4; package THT; pin spacing 400 mil; tolerance ±5%; resistance 470Ω
R3 | 2.49kΩ Resistor | power 3W; bands 4; package THT; pin spacing 400 mil; tolerance ±5%; resistance 2.49kΩ
R4 | 470Ω Resistor | power 3W; bands 4; package THT; pin spacing 400 mil; tolerance ±5%; resistance 470Ω
R6 | 470Ω Resistor | power 3W; bands 4; package THT; pin spacing 400 mil; tolerance ±5%; resistance 470Ω
R7 | 3.9kΩ Resistor | power 3W; bands 4; package THT; pin spacing 400 mil; tolerance ±5%; resistance 3.9kΩ
R8 | 470Ω Resistor | power 3W; bands 4; package THT; pin spacing 400 mil; tolerance ±5%; resistance 470Ω
R9 | 680Ω Resistor | power 3W; bands 4; package THT; pin spacing 400 mil; tolerance ±5%; resistance 680Ω
R10 | 1kΩ Resistor | power 3W; bands 4; package THT; pin spacing 400 mil; tolerance ±5%; resistance 1kΩ
R11 | 100kΩ Resistor | power 3W; bands 4; package THT; pin spacing 400 mil; tolerance ±5%; resistance 100kΩ
R12 | 680Ω Resistor | power 3W; bands 4; package THT; pin spacing 400 mil; tolerance ±5%; resistance 680Ω
R13 | 1kΩ Resistor | power 3W; bands 4; package THT; pin spacing 400 mil; tolerance ±5%; resistance 1kΩ
R14 | 100kΩ Resistor | power 3W; bands 4; package THT; pin spacing 400 mil; tolerance ±5%; resistance 100kΩ
R15 | 680Ω Resistor | power 3W; bands 4; package THT; pin spacing 400 mil; tolerance ±5%; resistance 680Ω
R16 | 1kΩ Resistor | power 3W; bands 4; package THT; pin spacing 400 mil; tolerance ±5%; resistance 1kΩ
R17 | 100kΩ Resistor | power 3W; bands 4; package THT; pin spacing 400 mil; tolerance ±5%; resistance 100kΩ
R18 | 680Ω Resistor | power 3W; bands 4; package THT; pin spacing 400 mil; tolerance ±5%; resistance 680Ω
R19 | 1kΩ Resistor | power 3W; bands 4; package THT; pin spacing 400 mil; tolerance ±5%; resistance 1kΩ
R20 | 100kΩ Resistor | power 3W; bands 4; package THT; pin spacing 400 mil; tolerance ±5%; resistance 100kΩ
R21 | 1kΩ Resistor | power 3W; bands 4; package THT; pin spacing 400 mil; tolerance ±5%; resistance 1kΩ
R22 | 470Ω Resistor | power 3W; bands 4; package THT; pin spacing 400 mil; tolerance ±5%; resistance 470Ω
R23 | 1kΩ Resistor | power 3W; bands 4; package THT; pin spacing 400 mil; tolerance ±5%; resistance 1kΩ
R24 | 1kΩ Resistor | power 3W; bands 4; package THT; pin spacing 400 mil; tolerance ±5%; resistance 1kΩ
R25 | 150Ω Resistor | power 3W; bands 4; package THT; pin spacing 400 mil; tolerance ±5%; resistance 150Ω
R26 | 680Ω Resistor | power 3W; bands 4; package THT; pin spacing 400 mil; tolerance ±5%; resistance 680Ω
R27 | 150Ω Resistor | power 3W; bands 4; package THT; pin spacing 400 mil; tolerance ±5%; resistance 150Ω
R28 | 680Ω Resistor | power 3W; bands 4; package THT; pin spacing 400 mil; tolerance ±5%; resistance 680Ω
R29 | 1kΩ Resistor | power 3W; bands 4; package THT; pin spacing 400 mil; tolerance ±5%; resistance 1kΩ
R30 | 1kΩ Resistor | power 3W; bands 4; package THT; pin spacing 400 mil; tolerance ±5%; resistance 1kΩ
R31 | 150Ω Resistor | power 3W; bands 4; package THT; pin spacing 400 mil; tolerance ±5%; resistance 150Ω
R32 | 150Ω Resistor | power 3W; bands 4; package THT; pin spacing 400 mil; tolerance ±5%; resistance 150Ω
R33 | 680Ω Resistor | power 3W; bands 4; package THT; pin spacing 400 mil; tolerance ±5%; resistance 680Ω
R34 | 680Ω Resistor | power 3W; bands 4; package THT; pin spacing 400 mil; tolerance ±5%; resistance 680Ω
R35 | 100kΩ Resistor | power 3W; bands 4; package THT; pin spacing 400 mil; tolerance ±5%; resistance 100kΩ
R36 | 100kΩ Resistor | power 3W; bands 4; package THT; pin spacing 400 mil; tolerance ±5%; resistance 100kΩ
R37 | 100kΩ Resistor | power 3W; bands 4; package THT; pin spacing 400 mil; tolerance ±5%; resistance 100kΩ
R38 | 100kΩ Resistor | power 3W; bands 4; package THT; pin spacing 400 mil; tolerance ±5%; resistance 100kΩ
R39 | 10kΩ Resistor | power 3W; bands 4; package THT; pin spacing 400 mil; tolerance ±5%; resistance 10kΩ
R40 | 10kΩ Resistor | power 3W; bands 4; package THT; pin spacing 400 mil; tolerance ±5%; resistance 10kΩ
R41 | 750Ω Resistor | power 3W; bands 4; package THT; pin spacing 400 mil; tolerance ±5%; resistance 750Ω
R48 | 100kΩ Resistor | power 3W; bands 4; package THT; pin spacing 400 mil; tolerance ±5%; resistance 100kΩ
R49 | 100kΩ Resistor | power 3W; bands 4; package THT; pin spacing 400 mil; tolerance ±5%; resistance 100kΩ
R50 | 1kΩ Resistor | power 3W; bands 4; package THT; pin spacing 400 mil; tolerance ±5%; resistance 1kΩ
R51 | 1kΩ Resistor | power 3W; bands 4; package THT; pin spacing 400 mil; tolerance ±5%; resistance 1kΩ
R52 | 150Ω Resistor | power 3W; bands 4; package THT; pin spacing 400 mil; tolerance ±5%; resistance 150Ω
R53 | 150Ω Resistor | power 3W; bands 4; package THT; pin spacing 400 mil; tolerance ±5%; resistance 150Ω
U1 | Voltage Regulator - 5V | voltage 5V; package TO220 [THT]; part # LM2940T-5.0
U2 | V18ZA2P | package v18za2p; part # ERZV14D220
Amount | Part Type | Properties
1 | Arduino Mega 2560 (Rev3) | type Arduino MEGA 2560 (Rev3); part # Arduino Mega 2560
5 | Ceramic Capacitor | voltage 6.3V; package 200 mil [THT, multilayer]; capacitance 0.1µF
5 | Ceramic Capacitor | voltage 6.3V; package 200 mil [THT, multilayer]; capacitance 0.22µF
4 | Ceramic Capacitor | voltage 6.3V; package 200 mil [THT, multilayer]; capacitance 1µF
2 | Ceramic Capacitor | voltage 50V; package 200 mil [THT, multilayer]; capacitance 0.1µF
1 | Tantalum Capacitor | voltage 10V; package 200 mil [THT, tantalum]; capacitance 47µF
1 | Tantalum Capacitor | voltage 35V; package 200 mil [THT, tantalum]; capacitance 10µF
1 | Ceramic Capacitor | voltage 6.3V; package 200 mil [THT, multilayer]; capacitance 0.3µF
1 | Ceramic Capacitor | voltage 6.3V; package 200 mil [THT, multilayer]; capacitance 0.01µF
11 | Schottky Diode | package 300 mil [THT]; type Schottky; part # 1N5818
4 | Rectifier Diode | package 300 mil [THT]; type Rectifier; part # 1N4004
1 | Zener Diode | power dissipation 0.5W; package 300 mil [THT]; type Zener; breakdown voltage 5.1V; part # 1N5919BG
2 | IC | chip label IC; true; package DIP (Dual Inline) [THT]; pin spacing 300mil; pins 8; hole size 1.0mm,0.508mm; part # TC4424EPA
1 | Dual VR Conditioner | chip label Dual VR Conditioner; true; package DIP (Dual Inline) [THT]; pin spacing 300mil; pins 8; hole size 1.0mm,0.508mm
1 | IC | chip label IC; true; package DIP (Dual Inline) [THT]; pin spacing 300mil; pins 8; hole size 1.0mm,0.508mm; part # TC4425EPA
1 | Screw terminal - 14 pins | package THT; pin spacing 0.197in (5.0mm); pins 14; hole size 1.5mm,0.508mm
3 | Screw terminal - 4 pins | package THT; pin spacing 0.197in (5.0mm); pins 4; hole size 1.5mm,0.508mm
1 | Screw terminal - 2 pins | package THT; pin spacing 0.197in (5.0mm); pins 2; hole size 1.5mm,0.508mm
3 | Generic female header - 3 pins | package THT; pin spacing 0.1in (2.54mm); row single; pins 3; form ♀ (female); hole size 1.0mm,0.508mm
2 | Generic female header - 2 pins | package THT; pin spacing 0.1in (2.54mm); row single; pins 2; form ♀ (female); hole size 1.0mm,0.508mm
8 | Red (633nm) LED | leg yes; package 5 mm [THT]; color Red (633nm)
1 | Generic female header - 6 pins | package THT; pin spacing 0.1in (2.54mm); row single; pins 6; form ♀ (female); hole size 1.0mm,0.508mm
1 | Schematic Frame | descr Inlet Air Temperature sensor; sheet 1/1; date 1404042789; filename Untitled Sketch 4.fzz
1 | Schematic Frame | descr Coolant Temperature Sensor; sheet 1/1; date 1404042789; filename Untitled Sketch 4.fzz
1 | Schematic Frame | descr Throttle Position Sensor; sheet 1/1; date 1404042789; filename Untitled Sketch 6.fzz; project Speeduino v0.2
1 | Schematic Frame | descr Battery Reference Voltage; sheet 1/1; date 1404042789; filename Untitled Sketch 4.fzz
1 | Schematic Frame | descr Injector 1; sheet 1/1; date 1404088041; filename schematic v0.2.fzz
1 | Schematic Frame | descr Sensor Screw connector 1; sheet 1/1; date 1404088363; filename schematic v0.2.fzz; project Speeduino v0.2
1 | Schematic Frame | descr Injector 3; sheet 1/1; date 1404088041; filename schematic v0.2.fzz
1 | Schematic Frame | descr Injector 2; sheet 1/1; date 1404088041; filename schematic v0.2.fzz
1 | Schematic Frame | descr Injector 4; sheet 1/1; date 1404088041; filename schematic v0.2.fzz
1 | Schematic Frame | descr O2 Sensor; sheet 1/1; date 1404042789; filename Untitled Sketch 6.fzz; project Speeduino v0.2
1 | Schematic Frame | descr Ignitor output 1; sheet 1/1; date 1404274298; filename schematic v0.2.fzz
1 | Schematic Frame | descr Ignitor output 2; sheet 1/1; date 1404274298; filename schematic v0.2.fzz
1 | Schematic Frame | descr Power supply; sheet 1/1; date 1404304523; filename schematic v0.2.fzz
1 | Schematic Frame | descr Crank and Cam sensors; sheet 1/1; date 1404042789; filename Untitled Sketch 4.fzz
1 | Schematic Frame | descr MAP sensor input; sheet 1/1; date 1405641290; filename schematic v0.2.fzz; project Speeduino v0.2
1 | Schematic Frame | sheet 1/1; date 1405660608; filename schematic v0.2.fzz
4 | Basic FET N-Channel | package TO220 [THT]; type n-channel; part # VND7NV04
2 | 2.49kΩ Resistor | power 3W; bands 4; package THT; pin spacing 400 mil; tolerance ±5%; resistance 2.49kΩ
5 | 470Ω Resistor | power 3W; bands 4; package THT; pin spacing 400 mil; tolerance ±5%; resistance 470Ω
1 | 3.9kΩ Resistor | power 3W; bands 4; package THT; pin spacing 400 mil; tolerance ±5%; resistance 3.9kΩ
8 | 680Ω Resistor | power 3W; bands 4; package THT; pin spacing 400 mil; tolerance ±5%; resistance 680Ω
11 | 1kΩ Resistor | power 3W; bands 4; package THT; pin spacing 400 mil; tolerance ±5%; resistance 1kΩ
10 | 100kΩ Resistor | power 3W; bands 4; package THT; pin spacing 400 mil; tolerance ±5%; resistance 100kΩ
6 | 150Ω Resistor | power 3W; bands 4; package THT; pin spacing 400 mil; tolerance ±5%; resistance 150Ω
2 | 10kΩ Resistor | power 3W; bands 4; package THT; pin spacing 400 mil; tolerance ±5%; resistance 10kΩ
1 | 750Ω Resistor | power 3W; bands 4; package THT; pin spacing 400 mil; tolerance ±5%; resistance 750Ω
1 | Voltage Regulator - 5V | voltage 5V; package TO220 [THT]; part # LM2940T-5.0
1 | V18ZA2P | package v18za2p; part # ERZV14D220

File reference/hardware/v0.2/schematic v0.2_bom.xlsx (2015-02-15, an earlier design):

QTY | Reference | My reference | Value | Type | Information | CTM QTY | Manufacturer | Model# | Digikey P/N | Each | CTM | Note
 | Capacitors
1 | C12,13,47,48 | C16 | 10uF | TANTALUM 10UF 35V 10% RADIAL, 0.098” LS | Tantalum | 4 | AVX Corporation | TAP106K035SCS | 478-1842-ND (http://www.digikey.com/product-detail/en/TAP106K035SCS/478-1842-ND/563945) | $1.62 | $1.62
5 | C1,2,3,4,5,8,20,27,30,31,37,38,44,51,55 | C2,4,6,8,10 | 0.22uF | CERAMIC 0.22UF 50V 10% RADIAL,X7R 0.098 LS | X7R | 15 | Kemet | C320C224K5R5TA | 399-4288-ND | $0.46 | $2.30
7 | C6,14,15,16,17,22,26,28,29,32,33,34,35,39,41,49,54 | C1,3,5,7,9,13,15 | 0.1uF / 100nF | CERAMIC 0.1UF 50V 10% RADIAL, 0.100” LS | X7R | 17 | Kemet | C320C104M1U5TA | 399-4264-ND | $0.22 | $1.54
1 | C18,19 | C14 | 47uF | TANTALUM 47UF 10V 10% RADIAL, 0.100” LS | Tantalum | 2 | AVX Corporation | TAP476K010SCS | 478-1910-ND (http://search.digikey.com/us/en/products/TAP476K010SCS/478-1910-ND/564013) | $1.65 | $1.65
1 | C21,56 | C18 | 0.33uF | CERAMIC 0.33UF 50V 10% RADIAL, 0.100” LS | X7R | 2 | TDK Corporation | FK14X7R1H334K | 445-5312-ND (http://search.digikey.com/us/en/products/FK14X7R1H334K/445-5312-ND/2256792) | $0.38 | $0.38
1 | C23,42,53 | C19 | 0.01uF | CERAMIC 10000PF 50V 10% RADIAL, 0.100” LS | X7R | 3 | Kemet | C315C103K5R5TA | 399-4148-ND (http://www.digikey.com/product-detail/en/C315C103K5R5TA/399-4148-ND/817924) | $0.31 | $0.31
4 | C36,43,52,57 | C11,12,20,22 | 1uF | CERAMIC 1UF 25V 10% RADIAL, 0.100” LS | X7R | 4 | Kemet | C315C105K3R5TA | 399-9714-ND | $0.79 | $3.16
 | Diodes/LEDs
1 | D2 | D16 | 5.6v 1w | DIODE ZENER 5.6V 3W AXIAL | DO-41 | 1 | ON Semiconductor | 1N5919BG | 1N5919BGOS-ND | $0.34 | $0.34
11 | D6,7,8,9,10,11,12,13,14,15,16,17,43,44,45,46,47,48 | D1,2,3,4,5,6,7,8,13,14,15 | 1N5818-TP | DIODE SCHOTTKY 1A 30V DO41 | DO-41 | 18 | Micro Commercial Co | 1N5818-TP | 1N5818-TPCT-ND (http://search.digikey.com/us/en/products/1N5818-TP/1N5818-TPCT-ND/950587) | $0.30 | $3.30
8 | D3,18,19,20,21,22,23,30,31,35,36,39,41 | LED1,2,3,4,5,6,7,8 | LED-Red | LED SS 5MM 625NM RED DIFF | 5mm-LED |  |  |  |  |  | $0.00
4 | D24,25,26,27,28,29,32,37,38,40,42,49,54 | D9,10,11,12 | 1N4004 | DIODE GEN PURPOSE 400V 1A DO41 | DO-41 | 13 | Micro Commercial Co | 1N4004-TP | 1N4004-TPMSCT-ND | $0.11 | $0.44
1 | MOV1 |  | Surge Protection | SURGE ABSORBER 14MM 22V 1000A ZNR | Disc 14mm | 1 | Panasonic - ECG | ERZ-V14D220 | P7307-ND (http://search.digikey.com/us/en/products/ERZ-V14D220/P7307-ND/227567) | $0.72 | $0.72
1 | L1 |  | 40 | Ferrite 1.5A 40 Ohm 0805 SMD | 0805 SMD | 1 | Laird-Signal Integrity Products | MI0805K400R-10 | 240-2389-1-ND | $0.10 | $0.10
4 |  |  | Jumper | SHUNT JUMPER .1" BLACK GOLD |  |  |  |  | 3M9580-ND | $0.12 | $0.48
 | Pin Headers
2 | Load1,P20,P21,P33,P34,JP1,JP2,PP1,PP2 | Male pins | 0.100 Pin Header | CONN HEADER 50POS .100" SINGLE GOLD |  | 1 | Samtec Inc | TSW-150-07-L-S | SAM1031-50-ND (http://search.digikey.com/us/en/products/TSW-150-07-L-S/SAM1031-50-ND/1101377) | $3.11 | $6.22 | Can be found much cheaper elsewhere
 | MOSFETs/Transistors
4 | Q1,2,3,4 | Q1,2,3,4 (v0.2.1 board) | VND7NV04TR-E | MOSFET N-CH 40V 6A VND7NV04TR-E 60mOhm | DPAK | 4 | STMicroelectronics | VND7NV04TR-E | 497-11714-1-ND (http://www.digikey.com.au/product-detail/en/VNN7NV04PTR-E/497-11714-1-ND/2746943) | $1.75 | $7.00
4 | Q1,2,3,4 | Q1,2,3,4 (v0.2 board) | STP62NS04Z | MOSFET N-CH 33V 62A TO-220 | TO-220 | 4 | STMicroelectronics | STP62NS04Z | 497-5896-5-ND | $1.79 | $7.16
 | Resistors
7 | R1,2,3,4,5,11,12 | R39, 40 | 10k | RES 10.0K OHM 1/4W 1% METAL FILM |  | 7 | Yageo | MFR-25FBF-10K0 | 10.0KXBK-ND (http://search.digikey.com/us/en/products/MFR-25FBF-10K0/10.0KXBK-ND/13219) | $0.08 | $0.56
32 | R7,13,16,17,18,19,21,22,41,42,43,44,45,46,54,56,59,60,70,71,74,77,78,80,81,83,84,87,88,95,104,105 | R10,13,16,19,23,24,29,30 | 1k | RES 1.00K OHM 1/4W 1% METAL FILM |  | 32 | Yageo | MFR-25FBF-1K00 | 1.00KXBK-ND | $0.06 | $1.92
17 |  | R9,12,15,18,26,28,33,34 | 680 | RES 680 OHM 1/4W 1% AXIAL |  | 17 | Yageo | MFR-25FBF52-2K43 | 2.43KXBK-ND | $0.08 | $1.36
17 | R8,9,10,47,48,49,50,51,52,53,55,61,62,66,67,72,75 |  | 2.43k | RES 2.43K OHM 1/4W 1% AXIAL
9 | R26,27,28,32,33,34,57,58,82 | R2,4,6,8,22, | 470 | RES METAL FILM 1/4W 470 OHM 1% AXIAL |  | 9 | Stackpole Electronics Inc | RNF14FTD470R | RNF14FTD470RCT-ND | $0.11 | $0.99
2 | R24,25,31 | For GM sensors | R1,3 | 2.49k | RES 2.49K OHM 0.25W 0.1% METAL FILM | For GM Sensors | 3 | TT Electronics/Welwyn | RC55Y-2K49BI | 985-1047-1-ND (http://search.digikey.com/us/en/products/RC55Y-2K49BI/985-1047-1-ND/2401912) | $1.92 | $3.84 | Only purchase if using GM Sensors
1 | R29 | R7 | 3.9k | RES 3.9K OHM 1/4W 0.1% METAL FILM AXL |  | 1 | Yageo | MFP-25BRD52-3K9 | 3.9KADCT-ND (http://search.digikey.com/us/en/products/MFP-25BRD52-3K9/3.9KADCT-ND/2059137) | $0.55 | $0.55
1 | R30 | R21 | 1.0k | RES 1K OHM 1/4W 0.1% METAL FILM AXL |  | 1 | Yageo | MFP-25BRD52-1K | 1KADCT-ND (http://search.digikey.com/us/en/products/MFP-25BRD52-1K/1KADCT-ND/2059121) | $0.55 | $0.55
17 | R14,15,35,36,37,38,39,40,63,68,69,73,76,89,90,102,103 | R11,14,17,20,35,36,37,38 | 100k | RES 100K OHM 1/4W 1% METAL FILM |  | 17 | Yageo | MFR-25FBF-100K | 100KXBK-ND (http://search.digikey.com/us/en/products/MFR-25FBF-100K/100KXBK-ND/13473) | $0.06 | $1.02
4 | R91,92,100,101 | R25,27,31,32 | 160 | RES 160 OHM 2W 1% AXIAL |  | 4 | Yageo | FMP200FRF52-160R | 160YCT-ND | $0.27 | $1.08
 | ICs
1 | U2,3 | U1 | LM2940T-5.0/NOPB | IC REGULATOR LDO LM2940-5.0 1A TO220 | TO-220 | 2 | Texas Instruments | LM2940T-5.0/NOPB | LM2940T-5.0/NOPB | $1.68 | $1.68
2 | U2,3 |  | 7721-7PPSG | INSULATING SHOULDER WASHER |  | 2 | Aavid Thermalloy | 7721-7PPSG | HS418-ND | $0.23 | $0.46
1 | U6 | MPX4250A |  | SENSOR ABS PRESS 36.3 PSI MAX | 6-SIP | 1 | Freescale Semiconductor |  | MPX4250AP-ND (http://www.digikey.com.au/product-detail/en/MPX4250AP/MPX4250AP-ND/464053) | $16.37 | $16.37
2 | U9,12 | IC1,2 | TC4424EPA | IC MOSFET DVR 3A DUAL HS 8-DIP | 8-DIP | 2 | Microchip Technology |  | TC4424EPA-ND | $1.98 | $3.96
1 | U10,14 | IC5 | TC4425EPA | IC MOSFET DVR 3A DUAL HS 8-DIP | 8-DIP | 1 | STMicroelectronics |  | TC4425EPA-ND | $1.96 | $1.96
1 |  | IC SOCKET MACH PIN ST 8POS TIN |  |  |  |  |  | AR08-HZL-TT-R | AE10011-ND
0 | Case | Case (TBA) |  | 3.12”x5.00”x1.85” Extruded Aluminum Split Body Case |  | 1 | Context Engineering Company | 3008H-5B (plain ends) or 3008F-5N (flanged ends) | http://store01.prostores.com/servlet/thescienceshop/the-2220/5.0%22-L-x-3.12%22/Detail | $14.99 | $0.00
 | Printed Circuit Board | Printed Circuit Board
1 | v0.2 | v0.2 | Estimate ONLY |  |  | 1 | N/A | N/A |  | $15.00 | $15.00
1 | Arduino Mega | Arduino Mega |  |  |  |  |  |  | 1050-1018-ND | 61.65 | $61.65 | Note that these can be found a lot cheaper elsewhere (~$25)
 |  |  |  |  |  |  |  | Total of Materials:Cost to Manufacture |  | US Dollars | $149.67 | Not including shipping or sales tax

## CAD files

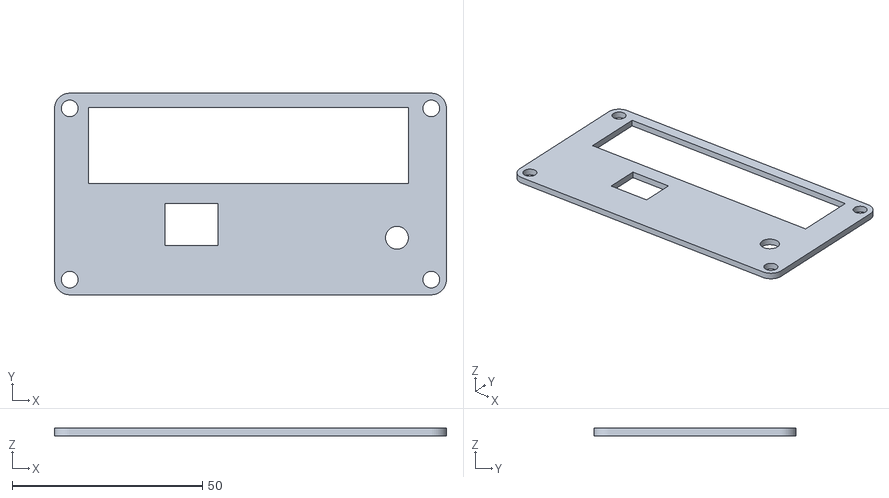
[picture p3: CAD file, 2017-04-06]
reference/hardware/Pro/Case/Endplate.stl
103.0 x 53.0 x 2.00

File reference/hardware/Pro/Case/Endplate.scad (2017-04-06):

$fn=50;
height=1;
hole_radius=(3.3782/2)+0.5;
corner_radius=4.00;
//hole_radius=(3.3782/1);

module plate()
{
    difference()
    {
        //Basic outline
        minkowski() {
            cube([95.02,45,height]);
            // rounded corners
            cylinder(r=corner_radius,h=height);
        }

        //Holes
        translate([0,0,-5])    cylinder(r=hole_radius, h=10);
        translate([0,45,-5])    cylinder(r=hole_radius, h=10);
        translate([95.02,0,-5])    cylinder(r=hole_radius, h=10);
        translate([95.02,45,-5])    cylinder(r=hole_radius, h=10);
        
        //USB cutout
        USB_height = 11;
        translate([-corner_radius+29.3,-corner_radius+13,-5])	cube([14,USB_height,10]);
        
        //MAP cutout
        //translate([20,110,screw_window_z+screw_window_height/2-2])	rotate ([90,0,0])   cylinder(r=3,h=screw_window_height);
        translate([-corner_radius+90,-corner_radius+15,-5])	cylinder(r=3,h=10);
        
        //Main loom cutout
        loom_width=84;
        loom_height=20;
        translate([-corner_radius+9,-corner_radius+29.2,-5])    cube([84,20,10]);
        

    } //difference()
}

//projection(cut = true) plate(); //2D projection
plate(); //3D model

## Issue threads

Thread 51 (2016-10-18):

Some ideas to improve the speed

tausday, 2016-10-18:
Hello,

I'm new at Speeduino and i have to admit that i don't understand really much, but i will try to help to make it better.

Now i will tell u, which ideas i have.
1. Increase the speed from the loop. The speed of the loop is slow because there is an overhead, if u write something like:

while (true)
    {
        // do stuff...
    }

The Loop will be in while and it will be much faster.
1.  Change from digitalWrite() to digitalWriteFast() thats an library which increase the speed by change the pin by manipulation.
   digitalWrite() = 6280ns
   digitalWriteFast() = 125ns
   I have read this article about the accuracy of the ignition timing.. maybe its makes better or did u have an correction factor for the slow pinchange.
   http://speeduino.com/forum/viewtopic.php?t=223

Question: Have u an idea why the ignition accuracy is jumping on high rpm?
-Stock micros resolution is to low?
-Stopping interrupts on some times are the reason?
Maybe its possible to fix the ignition accuracy to <1 degrees@8000RPM
I don't understand how u trigger the Ignition time, maybe u can help me by learning the code
1. sensors.ino
   There are some code what i not understand:
   For all sensors(TPS,CLT,IAT,O2,Bat) u read it first time without doing something with the value:
   Example;

```
analogRead(pinTPS);
byte tempTPS = fastMap1023toX(analogRead(pinTPS), 0, 1023, 0, 255); //Get the current raw TPS ADC value and map it into a byte
```

Why is the code "analogRead(pinTPS);" in row 92?? I don't understand why u do that, because in the next row u read it again.
1. Maybe its make faster if the ADC Ports run in free so the code will not be stopped just be interrupted.

I hope u understand me.

Best regards

tausday

<bountysource-plugin>

---
Want to back this issue? **[Post a bounty on it!](https://www.bountysource.com/issues/38468043-some-ideas-to-improve-the-speed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)** We accept bounties via [Bountysource](https://www.bountysource.com/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).
</bountysource-plugin>

VitorBoss, 2016-10-20:
If you look closer the code have a lot of analogRead() repeated for same input.

Thank you for digitalWriteFast() idea, I have tested it and is even more effective, it scores about 58 times faster. It's a wonder.

tausday, 2016-10-20:
thanks 4 response..
Victor can u tell me why there is an "standalone" analogRead? analogRead(pinTPS); i would be understand it and i can't sleep because that

noisymime, 2016-10-20:
With the 2 calls to analogRead, this is to ensure accuracy of the reading. When doing a number of calls to analogRead for different pins, you have to ensure that the internal sampling capacitor has enough to to full charge and hence get an accurate reading.
analogRead itself does not run for a fixed amount of time, it has a loop that tracks the status of this ADC read and returns when ready. The 2nd call to analogRead runs many many times faster than the first.

Just generally around performance improvements, there is a gauge you can view in TunerStudio that shows the loops per second that the arduino is performing. **This is the primary indicator of performance in Speeduino**. Load up a running test system (ie has an RPM input from something like ardustim and is outputting fuel/ignition pulses) and see what that gauge reads. Make a change somewhere in the code, upload it and see what difference it makes on that gauge.

VitorBoss, 2016-10-20:
For ensure s the accuracy is just decrease speed of readings, try to change it to 250ksps instead 1msps

noisymime, 2016-10-20:
The sampling frequency has no impact on the time it takes to charge the sample capacitor, that is purely electrical, based on the impedance of the circuit being measured and the current being fed to the ADC.

tausday, 2016-10-21:
Hello noisymime,

i have test now the while loop in the main loop at 7560 RPM+-8RPM

Normal Loop = 860Loop/s
While Loop    = 870Loop/s

Now i go to bed

VitorBoss, 2016-10-21:
Yes, has no impact on the time to charge the capacitor, but impact the successive approximation circuitry.

`By default, the successive approximation circuitry requires an input clock frequency between 50kHz and 200kHz. If
a lower resolution than 10 bits is needed, the input clock frequency to the ADC can be as high as 1000kHz to get a
higher sample rate.`
ATmega640/V-1280/V-1281/V-2560/V-2561/V [DATASHEET] page 271
version 2549Q–AVR–02/2014

VitorBoss, 2017-02-06:
Sorry for long delay, the digitalWriteFast() function have a problem with interrupts, there is another version to  handle this but return an error wen compiling

noisymime, 2024-03-15:
Closing as stale

Closed 2024-03-15.

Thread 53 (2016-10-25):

Analog readings

VitorBoss, 2016-10-25:
Using my last comment on issue #51

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

I think is better to use analog interrupt handle. Make a struct named AnChannel with all 16 channels.

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

This will speedup the analog conversions, at prescaler selected to clk/128 will run at 125KHz(limit due to page 271), is 8ms continuous conversion interrupt.

noisymime, 2016-10-26:
The interrupt is without a doubt a more efficient way to do the readings, but consideration needs to be given to how the code can be shared on other platforms (Such as Teensy). Keep in mind also that doing it this way will require some form of ADC queue as there will be multiple analog reads requested concurrently.

For what it's worth, my testing shows no discernible difference in ADC accuracy at 1Mhz vs 125Khz. The definitive comment on this is included in AVR120 application note (http://www.atmel.com/Images/doc2559.pdf):

> The ADC accuracy also depends on the ADC clock. The recommended maximum ADC clock frequency is limited by the internal DAC in the conversion circuitry. For optimum performance, the ADC clock should not exceed 200 kHz. However, frequencies up to 1 MHz do not reduce the ADC resolution significantly.

Given that most of the analog values are scaled to 8 or 9 bits, the impact of a 1Mhz ADC clock is not noticeable.

VitorBoss, 2016-10-26:
Reading both Tennsy(3.5 and 3.6) datasheet, both have an interrupt mode for analog conversions, and both have a dedicate DMA option to do this with up to 16bits resolution. See on Chapter 39, Memory map and register definition: ADC Status and Control Registers 1 (ADCx_SC1n) section

([http://www.nxp.com/files/32bit/doc/ref_manual/K66P144M180SF5RMV2.pdf](url)) for 3.6
([http://www.nxp.com/files/microcontrollers/doc/ref_manual/K64P144M120SF5RM.pdf](url)) for 3.5

On Teensy datasheet don't seems to need a complex interrupt handle at all, and both have hardware average function and can run ADC clock frequency up to 4MHz.
If the impact at 1MHz is not noticeable keep it.

Maybe creating a header file to process all that?

jakemoroni, 2016-10-26:
VitorBoss, I think there are some issues with the example code you posted, but I agree with the general concept. I do realize you probably wrote that just to get your point across and that it’s not final code.

Basically, I feel that the analog inputs should be handled as follows:

-	Have conversions be initiated asynchronously and periodically (i.e., not initiated via the main program thread)
-	Use the “conversion complete” interrupt to grab the data from the respective channel and store it to some shared memory
-	All “reads” of the channel would then be obtained by reading from the shared memory rather than the ADC data registers (no queue necessary, just a small critical region/barrier to ensure atomic access)

There are a few advantages to this approach, one of which being the fact that analog reads will now be deterministic in time (and also won’t block the main thread, assuming that the current code just uses the regular analogRead function). It will also lead to an overall performance increase since more things are happening in parallel.

This is basically what I think you are getting at. However, one of the issues in your example is that new conversions are initiated automatically while in free running mode, and the value of the ADMUX register is basically “latched” one clock cycle before a conversion finishes. (See page 274).

Therefore, you will need to implement some extra logic to properly determine which channel the interrupt was for.

Consider your example:

Before/on the first iteration, ADMUX is first set to channel 0, you kick off the sampling clock, then get an interrupt. This interrupt represents a completed sample for channel 0. Then, before exiting the ISR, you change ADMUX to channel 1. However, the next sample for channel 0 has already started (it was started automatically as soon as the last one finished). Therefore, the next interrupt that you receive will be for channel 0 _again_ since the value of ADMUX changed afterwards. However, you will mistakenly assume it to be channel 1 because you’re reading the ADMUX register to determine the channel.

Basically, for all but the first interrupt, I think the interrupt will represent a completed sample for the channel of (ADMUX – 1) (wrapped).

Also note that there are some errors in how you’re determining the channel. The 6th MUX bit (MUX5) is actually in the ADCSRB register, not the ADMUX register. You’ll need to manipulate both of those.

I haven’t actually tested this, so forgive me if I’m wrong.

Thanks,
Jake

VitorBoss, 2016-10-27:
Yes Jake, it is a sketch, only to express my idea. I had read the related pages. Thank you for the MUX5 related mistake, I will try to fix that in following code.

ADCSRA register bit 4(ADIF) is messing with my head, on page 274 for a safely update says:

1. When ADATE or ADEN is cleared
2. During conversion, minimum one ADC clock cycle after the trigger event.
3. After a conversion, before the Interrupt Flag used as trigger source is cleared.

When updating ADMUX in one of these conditions, the new settings will affect the next ADC conversion.

But on page 285 says:
"ADIF is cleared by hardware when executing the corresponding interrupt handling vector. Alternatively, ADIF is cleared by writing a logical one to the flag."

> ADMUX = 0x01000000; //Starting at channel 0
ADCSRB = 0x00000000; //ADC Auto Trigger Source is in Free Running mode
//ADCSRB = 0x00000100; //ADC Auto Trigger Source is Timer/Counter0 Overflow
//ADCSRB = 0x00000110; //ADC Auto Trigger Source is Timer/Counter1 Overflow
ADCSRA = 0x11101100; // ADC Interrupt Flag enabled and prescaler selected to 1MHz
.
.
.
ISR (ADC_vect)
{
byte nChannel;
ADCSRA = 0x11001100; // ADC Auto Trigger disabled by clearing bit 5(ADATE)
nChannel = (ADMUX & 7);
if((ADCSRB & 0x00001000) { nChannel+=8; } //8 to 15
AnChannel(nChannel) = ADCL | (ADCH << 8);
if(nChannel==15) //channel 15
{ ADMUX = 0x01000000; } //channel 0
else if (nChannel==7) //channel 7
{
ADMUX = 0x01000000;
ADCSRB = 0x00001000; //Set MUX5 bit
}
else
{ ADMUX++; }
ADCSRA = 0x11101100; // ADC Interrupt Flag enabled
}

Maybe work, I will try it later.

VitorBoss, 2016-11-03:
with this:
>  ADMUX = 0x40; //Starting at channel 0
  ADCSRB = 0x00; //ADC Auto Trigger Source is in Free Running mode
  //ADCSRB = 0x04; //ADC Auto Trigger Source is Timer/Counter0 Overflow
  //ADCSRB = 0x06; //ADC Auto Trigger Source is Timer/Counter1 Overflow
  ADCSRA = 0xED; // ADC Interrupt Flag enabled and prescaler selected to 500KHz
ISR(ADC_vect)
{
  byte nChannel;
  int result = ADCL | (ADCH << 8);
  ADCcount++;
  ADCSRA = 0xCD; // ADC Auto Trigger disabled by clearing bit 5(ADATE)
  nChannel = ADMUX & 0x07;
  if(ADCSRB & 0x08) {nChannel+=8;} //8 to 15
  if(nChannel==0) {AnChannel[15] = result;}
  else {AnChannel[nChannel-1] = result;}
  if(nChannel==15)
  {
    ADMUX = 0x40; //channel 0
    ADCSRB = 0x00; //clear MUX5 bit
  }
  else if (nChannel==7) //channel 7
  {
    ADMUX = 0x40;
    ADCSRB = 0x08; //Set MUX5 bit
  }
  else {ADMUX++;}
  ADCSRA = 0xED; // ADC Interrupt Flag enabled
}

I got:
2500 Loops with Clean code and interrupts: 30704
 A0=963 A1=904 A2=844 A3=783 A4=723 A5=664 A6=602 A7=542 A8=481 A9=421 A10=360 A11=300 A12=240 A13=179 A14=119 A15=58
Number of analogic interrupts: 1179

This changing ADCSRA = 0xCC (prescaler selected to 1MHz) :

2500 Loops with Clean code and interrupts: 57164
 A0=930 A1=903 A2=843 A3=783 A4=723 A5=663 A6=601 A7=542 A8=481 A9=421 A10=360 A11=300 A12=240 A13=179 A14=119 A15=57
Number of analogic interrupts: 4395

and this changing bit ADCSRA = 0x6C and this code:

> //if(nChannel==0) {AnChannel[15] = result;}
  //else {AnChannel[nChannel-1] = result;}
  AnChannel[nChannel] = result;

2500 Loops with Clean code and interrupts: 27748
 A0=956 A1=897 A2=838 A3=777 A4=719 A5=660 A6=600 A7=542 A8=483 A9=425 A10=365 A11=305 A12=245 A13=185 A14=125 A15=63
Number of analogic interrupts: 880

VitorBoss, 2016-11-03:
PS. using 220R resistors from 5V to channel A0, 220R to A1 ... A15 to GND,

VitorBoss, 2016-11-05:
Codding done, now are working with main code.

Closed 2016-11-05.

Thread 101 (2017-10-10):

Rover MEMS pattern

noisymime, 2017-10-10:
Per thread: https://speeduino.com/forum/viewtopic.php?p=21572&sid=e3841610b755204f35a86d9cf3f43041#p21572

32 poles spaced at 10 degree intervals, with 4 missing poles,at 30, 60,210 and 250 degrees.

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

<bountysource-plugin>

---
Want to back this issue? **[Post a bounty on it!](https://www.bountysource.com/issues/50136565-rover-mems-pattern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)** We accept bounties via [Bountysource](https://www.bountysource.com/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).
</bountysource-plugin>

Autohome2, 2017-11-17:
further information on this trigger pattern
[mems3 crank and cam.pdf](https://github.com/noisymime/speeduino/files/1481867/mems3.crank.and.cam.pdf)

andymcg85, 2018-03-18:
Following for updates.

yeco, 2018-03-19:
Following.

mapgdb, 2020-06-09:
Any progress? Looking into starting my own Speeduino project and this would help out!

mike501, 2020-10-27:
Rover have multiple mems trigger patterns from what I can gather. I'm aware of 3 and their maybe a 4th!
So far I've got,
Pattern 1 36-1-1        (17 teeth - gap - 17 teeth - gap)
Pattern 2 36-1-1-1-1 ( 13 teeth - gap - 2 teeth - gap - 14 teeth - gap - 3 teeth - gap)
Pattern 3 36-1-1-1-1 ( 11 teeth - gap - 5 teeth - gap - 12 teeth - gap - 4 teeth - gap)

The 'maybe' pattern i can't find anymore but it think it was a variation on mode 2 & am hopeful it was someone looking at the same wheel differently.

I've asked the person who said they had a working pattern to post up their details. If it works, i'll steal it to make the alternate pattern. If they don't post i'll look to create the patterns.

Pattern 1 is really a 18 - 1 at double crank speed. I'm curious if you could get away saying its the cam signal intead of crank.
Pattern 2 and 3 i'm wondering if I could 'cheat' and count teeth. Once I find (pattern 2) 14 teeth or (pattern 3) 12 teeth i know where i am on the crank.

I don't have details on the cam sensor and its relation to the crank - hence can't do that.
I've attached the spreadsheet i've created with the teeth mappings in for ardustim.
[rover mems trigger pattern.xlsx](https://github.com/noisymime/speeduino/files/5445299/rover.mems.trigger.pattern.xlsx)

james-portman, 2020-11-08:
Clearer picture below of the original flywheel the creator is talking about, "Pattern 2" as Mike above has written about.

It would be good to get pattern 1 & 2 working as above for the Rover Minis to provide a cheaper alternative to current ECU swaps.
I don't mind having a go at this if nobody else gets it working first.

I think..
Pattern 1 - for cars with (ECU timed) distributors to send the spark going to the right cylinder, and single point injection.
Pattern 2 - for cars with wasted spark coil packs. Single point injection without a cam sensor, can be multi point with a cam sensor.
Pattern 3 - same as 2

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

andymcg85, 2020-11-08:
I did a rover k series turbo conversion and I don't know if it's a simpler
option altho it was for me as it was several years ago and no body wanted
to create the trigger pattern. I welded a 36th wheel to the back of crank
pulley and it worked a treat

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

james-portman, 2020-11-08:
Can anyone direct me a bit?
If I make new code then I have a Mega here I can test it on, I got that up and running in tunerstudio.
If I get another arduino to pretend to be the crank signal, which pin on the mega is it?

I tried to look through the init code but it gets a bit wild..

james-portman, 2020-11-09:
Started code (without cam support) here:
https://github.com/noisymime/speeduino/compare/master...james-portman:rover-36-1-1-1-jamesp?expand=1
Working for JDM Mini SPI flywheel pattern perfectly.

Could be possible to adapt slightly to fit many cars with multiple gap pattern flywheels, at least the other Rover flywheels and add cam support

Closed 2023-04-30.

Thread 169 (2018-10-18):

Strange basic distributor behavior

jmunkdk, 2018-10-18:
Hello,

I have for as long as I have attempted to get the Speeduino working on my 1975 VW Bus had issues starting it. Now that the weather is colder it is basically a no go, so I decided to check the starting attempt with a logic analyzer. There is certainly something wrong, and both ignition and injection seems rather random.

The trigger is a hall sensor in a basic distributor (with advance locked). The distributor is an original electronic Bosch from a slightly newer VW, but is working perfectly.

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

[VW start 01.zip](https://github.com/noisymime/speeduino/files/2493334/VW.start.01.zip)
(PulseView from http://sigrok.org. Can provide other formats)

As you can see it is firing and injecting all over, which is rather odd since "Fix cranking with trigger" is on. Only slightly special observation is that the cranking speed is not very high for these old VW engines, but this is normal. They are also normally very easy starters, and this is probably why I have been able to start it at all. Anyway, all other details should be in the tune file, or ask.

[CurrentTune.zip](https://github.com/noisymime/speeduino/files/2493307/CurrentTune.zip)

Besides reporting this issue, I wonder if a 36-1 missing tooth trigger like this would resolve the issue:

http://thedubshop.com/type-4/

Thanks,

Jens.

<bountysource-plugin>

---
Want to back this issue? **[Post a bounty on it!](https://www.bountysource.com/issues/64944297-strange-basic-distributor-behavior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)** We accept bounties via [Bountysource](https://www.bountysource.com/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).
</bountysource-plugin>

PSIG-dev, 2018-10-19:
I assume you are using the latest AUG18-2 firmware and INI?  There may be a code issue, but your trigger signal is rather messed-up.  Not just slow.  If you can fix that, it would make diagnosing any ECM issues easier.  Please post a short log of engine starting using your current tune.

If you tested the trigger (tach) signal at Speeduino input, please test again at the D19 pin on the MEGA, or other nearby place on the board, such as IC3 pin 8 hole.  Compare with a test directly at the sensor connector.  This will narrow the source of the weird distributor signal.  Are you using any type of signal conditioning circuit?  This is not possible if working correctly:
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
Perhaps posting all of this in your forum project thread would be more effective.

jmunkdk, 2018-10-19:
Requested new measurements are ready. The zip file contains the tune, and a set of a MT log and a logic analyzer log. Just to be absolutely sure there is no noise sources, I have disconnected injectors, ignition coil, ICV and fuel pump. The trigger is measured at IC3 pin 8, and it is clean. The sample rate is 16 MHz, so nothing should be missed. The pulses match the RPM in the TS log of about 134 rpm on average, so it must read them correctly. Ignition and injection only seems sporadically correlated to the trigger.

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

[WV Start 02.zip](https://github.com/noisymime/speeduino/files/2496101/WV.Start.02.zip)

What do you think?

PSIG-dev, 2018-10-20:
Yes, your second LA image shows a much cleaner and more consistent trigger pulse, with a different system response.  This will make some diagnoses by @noisymime much easier, but also means you have some signal cleaning to do (likely identifying EMI to fix or avoid, based on the signal changes).

The "after-run" pulses are _generally_ not an issue, as either or both Speeduino and the components (ignition, injectors, etc) are not powered or power is removed when keyed-off.  Speeduino is attempting to predict proper spark and fuel with last-known information, while still powered and functional.  In other situations (e.g., engine stall), the RPM reduces (even if very quickly) and after-run pulses are not an issue _that I have seen_.  If you have a situation where trigger pulses stop instantly, but the Speeduino and the components remain powered, and after-run pulses continue in a potentially damaging way; please describe it so that appropriate solutions may be pursued.

jmunkdk, 2018-10-21:
Thanks,

After my last post, I did some more measurements, and most notably it appeared that the trigger filter was set to OFF. This is the default setting in speeduino.ini, so I suggest you change that default to Medium.

Setting the trigger filter to medium seems to get fairly solid ignition and injection pulses, but it now takes between a couple of trigger pulses to 5 - 10 trigger pulses before it starts to ignite and inject. One time it didn't start pulsing at all. Skip revolution cycles (1 and 0 tried) doesn't seem to make any particular difference and changing the trigger angle between -5, 0 and 180 neither.

The description of "Fix cranking timing with trigger" says "On certain low resolution ignition patterns, the cranking timing can be locked to occur when a pulse is recieved.", but it doesn't seem to make any difference either.

The New Ignition mode left one of the injectors permanently on when I stopped cranking!

I see your point in the after cranking pulsing not being relevant, since you turn it all off. Well I then certainly need to get accustomed to turn the the key all the way to off when it doesn't start. Not too crazy about this, but OK, I can live with it for now.

So I think some more optimization is required for the simple distributor mode.

Having said all that, how will a 36-1 hall trigger work in this respect? Any trigger guessing? Any after crank pulsing?

Thanks,

PSIG-dev, 2018-10-22:
Good suggestion — we can ask for outputs to be clipped/cut after a limited or configurable time in cranking mode.

The trigger filter is default to "Off", assuming a clear and clean signal.  Which setting to use if yours is not is then up to you, as (like you've seen) it carries compromises, and each situation is different.

@noisymime should perhaps have a look at "Fix cranking timing with trigger", as it should clearly be _**if A then B**_, where an input signal directly results in an output.  There are others using Basic Distributor in this way without claimed issues, so I'm not sure of the differences you are seeing.

Low-resolution timing control is extremely challenging.  Consider an analogy, where you are playing ball with someone, and you know they are going to throw the ball sometime, but you only get to look for a moment every few seconds.  Good luck... LOL  A 36-1 would have greater resolution and fewer potential issues trying to time spark outputs.  There is little 'guessing' for setup.  'After-pulsing' would be the same as currently.

TBAMax, 2021-10-12:
Just a note here for now. Recently I discovered that there is a problem with  "per tooth ignition"  running with "fixed cranking ignition override". Should be one or another but not both.

noisymime, 2024-03-14:
Closing this as stale. I believe this has likely been addressed in other changes that have gone in for this decoder over the past few years.

If this remains a problem, please create a new issue for this.

Closed 2024-03-14.

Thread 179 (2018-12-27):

Vbat voltage correction/offset

PSIG-dev, 2018-12-27:
Feature request of a voltage offset/correction, adjusted in TunerStudio, between a meter reading at the Speeduino input and the reported battery voltage by Speeduino.  Perhaps a simple slider to adjust until the voltage readings match.  No other curves or compensation.  This would allow corrections due to inherent error in Arduino internal voltage or regulator reference, but also allow offsets such as adding inline reverse-polarity diode/transistor protection with an offset for true system voltage, allowing proper application of voltage corrections (injector latency, coil dwell, etc).

<bountysource-plugin>

---
Want to back this issue? **[Post a bounty on it!](https://www.bountysource.com/issues/67996481-vbat-voltage-correction-offset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)** We accept bounties via [Bountysource](https://www.bountysource.com/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).
</bountysource-plugin>

Tobbera, 2019-04-27:
Good idea! I'm altering sensors.ino at the moment.

`tempReading = fastMap1023toX(AnChannel[pinBat-A0], 162); //Get the current raw Battery value. Permissible values are from 0v to 24.5v (245)`

Replace 162 to match your true voltage.

noisymime, 2019-07-01:
Playing around with this at the moment and there's the question of whether the adjustment/offset should be % based or a fixed voltage offset. From the testing I've done, a fixed offset voltage seems to work well, but I thought I'd check and see whether there are any known use cases that would require a % adjustment instead.

Tobbera, 2019-07-05:
I have never used % adjustment. Static ADC read value is what I have had luck with. But there might be need for both in the case of a diode and voltage divider. First 0,5V off in the diode then percentage on the voltage divider,

PSIG-dev, 2019-07-05:
Agreed on the basis that most issues are based on general offset for the majority, and while drop may change with current, % would improve dynamic precision.  That would be gravy.  So either approach could work, with a basic offset value for measured difference under typical conditions; or a % that gives same result but (hopefully) remains correct with minor offset changes.  I think the first goal is a general correction to avoid most secondary issues and effects, but if % will help or not hurt (cause worse errors in certain circumstances) in achieving that goal, then go for it.

noisymime, 2019-07-08:
I've pushed a change which has this as an absolute correction value. Have a play and see if it works like that and if not comment and I'll open it back up to add a % variation as well

Closed 2019-07-08.

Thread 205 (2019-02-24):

No fuel pump priming pulse if you have USB connected prior to starting car

ESDave05, 2019-02-24:
This is probably getting a bit pedantic but just an observation:

My typical workflow for tuning the MX5 would be:

Key out
Connect laptop to Speeduino, start tuner studio
Turn ignition on
Check sensors for valid readings etc...
Start Log
Start Engine

I notice i don't get the 5 second long fuel prime - I haven't dug into the code but assume it's in some initialization code that run when the USB was first connected - from there the Arduino does not go through a reset with key on / off.

Easy enough work around, just an observation. I often don't work on my car for months at a time so I would imagine fuel lines need a decent prime - a poor start due to no prime could be mis interpreted as a red herring tuning issue etc...

ric355, 2019-02-24:
Indeed this is because the arduino gets powered up when the USB line is connected, and hence the initialisation happens before you give power to the fuel pump via ignition.

As speeduino does not have an ignition on input, it isn't possible to move the priming pulse out of the initialisation code, although I suspect it would be a relatively easy mod and firmware change to achieve it.

noisymime, 2019-02-24:
Yeah, this is working 'as designed' as the intent is to prime only when the unit is powered on.

That said, this comes up quite often as a question, so I think it might be time to change that behaviour. I'm going to mark this as a feature request and look at changing it shortly, it should be very straightforward.

brunob45, 2019-02-25:
[brainstorming] A potential solution would be to start the fuel priming only when the speeduino first sees at least 12v on the battery voltage.

noisymime, 2019-02-25:
Yeah, the check itself for this is relatively straightforward, in basic pseudo code:

`if $current_voltage < 5.5 and $new_voltage > 7 then prime_pump()`

This would be in addition to the existing startup priming routine. Basically if the voltage was less than 5.5, the system was likely to have been on USB. If the voltage has now gone above 7 (The minimum dropout voltage for the regulator) then it's likely that the ignition has been turned on.

There's a little more error checking logic to add, but this is the high level of it.

ric355, 2019-02-25:
There are some other events that are also associated with key-on such as stepper homing. Would the intent be to include those as well?  Stepper is a good example of where the system does not behave properly if you connect the USB first, as it'll carry out the homing event without moving the stepper given no 12v is present. This in turn gets the stepper position immediately out of sync.

My concern about using input voltage is that transient voltage drops could generate false positives and cause the priming event (and any others we associate with it) to happen. Since the end of the priming event is to switch off the fuel pump we'd have to be careful to ensure this doesn't happen if a transient drop occurs while the engine is running.

Perhaps put it on a TS setting so that anyone who has problems can disable it.

noisymime, 2019-02-25:
Adding an RPM check definitely makes sense if the stepper is being added, which seems like a reasonable idea.

Even with the voltage though, if you're checking that it was previously <7v, then that generally should be sufficient. If the system voltage was below 7v and there wasn't USB connected, then the unit has very likely reset anyway due to the regulator dropout voltage being about 7v.

With the RPM check though (ie only do this if `rpm == 0`) then it should be safe.

ric355, 2019-02-28:
I have a prototype available for this one; I've done a bunch of bench testing on it and am going to test on the car later today. I should be able to submit a pull request in few days if you wish. No problem if you've already worked on it.

noisymime, 2019-02-28:
It's not fully tested, but I just pushed up the basic stuff that I put together around this. It seems to work, but it can be dependant on the filter value of the battery ADC, so I need to keep having a bit of a play around

ric355, 2019-02-28:
My solution is here:

https://github.com/ric355/speeduino/commit/5984e7fd98da23f2045d75edcab6e1ce185f7750

I also added an output channel so you can see the stepper priming event in TS using an indicator;

https://github.com/ric355/speeduino/commit/dd031771a028021964309f4263d797e7c245e298

I successfully tested it on the car today.

I did a similar thing regarding the battery threshold, but I did it in a different place and did not use a gap (your 55 to 70). I just said if it goes from < 70 to >= 70 then that is the trigger. This is because the ADC filtering setting has a big effect on the values you see within readBat as the voltage rises.

ESDave05, 2019-03-04:
Just an interesting observation, i actually get a phantom prime during ignition transition for 350ms.

I think it might be an RPM glitch detected as engine running, but RPM is flatline in datalog. Happens in the car and on the bench.

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

ToxicAvenger, 2019-05-03:
@ESDave05
Did you solve your problem with phantom prime pulses?
I'm observing something similar in my setup. After configuret period the pump goes off. Then it turns on again and turns off. I hear, that relay is clicking. The rpm log in TS is flat.

ESDave05, 2019-05-05:
I'm happy to keep it as a "feature" :) but for me it only happens once on Ignition transition.

turboedge, 2022-05-04:
Was this ever added to the firmware? I've had reports of it also playing heck with stepper idle valve homing.

noisymime, 2022-05-05:
Yeah, this has been in the firmware since e8c31d5ce743b3502395b9c48d6324dd6ecf5c78 though only for the fuel pump priming, not intending to cover stepper homing etc.

Worth nothing is that it is somewhat hardware dependent as well, requiring the USB line to backfeed onto the main power line when 12v is not connected. Most basic LDOs will do this, but not all and other power regulator designs (Eg switching regulators) will not necessarily work.

noisymime, 2024-03-15:
Closing as no further action is intended on this.

Closed 2024-03-15.

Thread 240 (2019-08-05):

Cranking Bypass does not fall back to cranking mode

turboedge, 2019-08-05:
When using cranking bypass the output correctly transitions from cranking mode to running. However if the engine stalls the output should immediately go back to the cranking mode like it is when you first turn the key to the on position.  Unfortunately this seems to only happen less than half the time, the rest of the time the output stays in the running mode.

My engine will restart because Speeduino works to control the timing itself, but in my case I am using the output for two purposes. The other to control the wide-band heater. So I would like it if it would turn off so that the wide-band shuts down when the engine is not running as intended.

Thanks!!

brunob45, 2019-08-05:
With the current code, the bypass will only reset when the speeduino reads an RPM between 0 and cranking RPM limit, which seems to happens not so often.
A quick fix would be to add the line
`if(configPage4.ignBypassEnabled > 0) { digitalWrite(pinIgnBypass, LOW); }`
under line 134 of speeduino.ino.
This will make the bypass output go LOW while the engine is stopped.

noisymime, 2019-08-05:
Yeah that was pretty much exactly what I was thinking, should be very straightforward. I'll test it tonight and get it added.

noisymime, 2019-08-05:
Hmmm, so I went to add this and then realised that the existing code actually works the opposite way around.

`if(currentStatus.RPM > currentStatus.crankRPM) //Crank RPM in the config is stored as a x10. currentStatus.crankRPM is set in timers.ino and represents the true value
        {
          BIT_SET(currentStatus.engine, BIT_ENGINE_RUN); //Sets the engine running bit
          //Only need to do anything if we're transitioning from cranking to running
          if( BIT_CHECK(currentStatus.engine, BIT_ENGINE_CRANK) )
          {
            BIT_CLEAR(currentStatus.engine, BIT_ENGINE_CRANK);
            if(configPage4.ignBypassEnabled > 0) { digitalWrite(pinIgnBypass, HIGH); }
          }
        }
        else
        {
          //Sets the engine cranking bit, clears the engine running bit
          BIT_SET(currentStatus.engine, BIT_ENGINE_CRANK);
          BIT_CLEAR(currentStatus.engine, BIT_ENGINE_RUN);
          currentStatus.runSecs = 0; //We're cranking (hopefully), so reset the engine run time to prompt ASE.
          if(configPage4.ignBypassEnabled > 0) { digitalWrite(pinIgnBypass, LOW); }
        }`

When the engine is cranking, the output goes LOW, and when it's running it goes HIGH. This seems backwards to me, but I can't recall now whether it was done for a specific reason.

There's actually a setting in the .ini file called `ignBypassHiLo` that looks like it was going to be for setting this direction, but it was never actually used.

@turboedge Does that match the behaviour you're seeing at the moment?

turboedge, 2019-08-06:
Yes, when key on engine off it starts out low and goes high when the engine starts. The GM late model HEI apparently works at logic level this way. You are right, it seems a bit backwards, but is how it works. I have re-purposed the second ignition channel driver for this instead of using the arduino output directly.

When the engine falls out of the running state, without turning the key off, it only rarely brings the output back to low.

brunob45, 2019-08-06:
This would be a nice opportunity to use a "state machine". It is an easy way to track actions to do on state change (cranking->running, running->stalled).

Closed 2019-08-06.

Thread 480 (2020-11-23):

Injector lag time - can be improved?

XPbIM3, 2020-11-23:
I have two things to ask about injector lag timing:

1. We have an opening lag time vs voltage calibration curve but have no handy tool to obtain correct values.  I do know two methods to obtain correct lag on working engine within diffirient voltages onboard:
  - track an AFR miss (% correction required) when targeting different AFRs  on idle
  - do a switchover between 1-2-4 pulses per cycle - resulting AFR should be somewhat close with correct lag time  - but speeduino requires a full restart when changing inj pulses per cycle. Also changing an injector time also requires full restart -   not so comfy. Can this be improved to have a tool to online calibrate lag time?

2. Injectors may have several other factors to consider when calculating lag time:   lag time vs voltage(lower V - harder to open - done),   lag time vs ramp pressure (higher MAP readout - more pressurized fuel in ramp - harder to open inj - more lag time),   some injectors may have "lag vs temperature" drift - mine do,  thats can be considered as  "lag time vs  fuel temp".
Also... it seems we have 0.1ms lag time precision in speeduino,  is this really enough?

pazi88, 2020-11-23:
0.1ms is plenty accurate because of the voltage correction. Lets say you have dead time of 0.101ms at 12v. Just put 0.1ms as dead time and 101% as voltage correction for 12v and that equals to 0.101ms

muuris, 2020-11-23:
Injector pressure does affect dead time, but it is assumed you input the values measured/know with your used fuel pressure. The pressure ratio across injector (fuel rail to manifold) should be constant, that's why the pressure regulator is for and no correction on dead time is required while running. This assumes of course you use MAP-referenced regulator.

The best way is to test injectors with different pulsewidths (with known voltage, pressure ratio and pulse count). This feature is currently not in firmware, but is quite easy to implement.

XPbIM3, 2020-11-23:
Pressure across injector is a constant - missed that moment ,  that's correct.

Closed 2022-01-05.

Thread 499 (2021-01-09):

External baro input doesn't work

TrinomCZ, 2021-01-09:
Hi,
during testing of black STM32F407VE6 board has been discovered, that external baro input doesn't work. When I tried to swap pins between various inputs, the problem moved with the baro pin, so it's clearly a SW issue.
External baro input has been enabled and input pin in TunerStudio has been always selected accordingly to what I had in init.ino file (there is no "board default" in this drop-down menu).
This issue seems to be present in all SW versions including the latest one (2020-12).

noisymime, 2021-01-09:
What is your hardware setup for this? I have many boards here with external bar sensors that are working without issues using a 2560, so I would be surprised if it's an issue in the firmware, but it maybe something specific to your hardware setup.

TrinomCZ, 2021-01-10:
Hi, I have just bare black STM32 development board with a potentiometer connected to whatever input pin I need to test.
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
In Speeduino file init.ino, it uses case 60, where on line 2075 is `pinBaro = PB1;`. As I mentioned in the first post, if I swap this to let's say PC1 and what used to be assigned to PC1 is now assigned to PB1, the problem moves around. At this moment, everything is back to default.
In tunerstudio, I can clearly see, that even though I have set baro input to external source, it still ignores these settings and baro value just jumps around MAP value (no, it definitely isn't a floating average of MAP).
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
At this moment, there is no RPM input and baro input pin is tied to ground.

noisymime, 2021-01-10:
You've got `PB1` selected in tunerStudio as the pin, but that isn't one of the options in the ini file. If you've modified that file, have you verified that the entry you've got there for `PB1` matches the actual pin number?

You can't just add `PB1` to the list in any place, its location in the array represents the pin number that will be used.

TrinomCZ, 2021-01-10:
Oh, I haven't realised, that I copied that whole line from an older ini file, because it lacks the "board default" option. I clearly recall, that using any of the "Axx" bricks my STM board and I had to manually erase the external flash in the past :(
I've put the line with Axx back in the ini file, but that doesn't solve my issue, so what would you recommend? Could you please point me out, where this input is being processed in the speeduino ino files to help me understand, which input should I use or how to force it to use "board default" setting, which is defined in init.ino?
Thank you.

TrinomCZ, 2021-01-21:
Any updates or ideas?

VitorBoss, 2021-01-21:
First, the arduino way for read analog channels listed on Tuner Studio won't work.
Second, the pin numbers must follow the library standard listed at https://github.com/stm32duino/Arduino_Core_STM32/blob/master/variants/BLACK_F407XX/variant.cpp#L49

Please keep the USB D lines out of listing, selecting them shouldn't hang the code anymore, but is safer to keep them out

TrinomCZ, 2021-01-21:
Victor, could you please try to explain it more in detail? Why every single analog input works, except for the baro input? If you say, it doesn't work in tunerstudio, how is the pin, which I can select in Tunerstudio transmitted to Speeduino and then translated into analog inputs? I'm asking, because I didn't fully understand the code, however selecting any of the Axx inputs causes STM board to brick. To unbrick it, I have to manually delete whole flash memory, otherwise it won't work (the port addressing is clearly wrong).
From my point of view (which might be wrong), I need to either force Speeduino to use the predefined input and totally ignore any settings comming from Tunerstudio or send the correct input from the Tunerstudio in the first place (which will be accepted by Speeduino).

In the past, I discussed this in the STM32 development thread and I saw someone modifying the speeduino.ini file for TS to include the PB0, PB1,... along the original A0, A1,... and they claimed, it works for them, so I did the same. Also this is the only way, how I was able not to brick my board, when I turned on the external baro input, though it didn't work.

TrinomCZ, 2021-02-09:
I see no response here, so I tried putting everything back to default (including the ini file for Tuner Studio) and flashed the chip again. I tried to select the A9 option, because that seems to be the right one for PB1 of my STM32 board (according to "board_stm32_generic,h"). This time, selecting the A9 didn't brick the board (heureka!), but also didn't do anything. I tried other inputs, but without any success. Then I've discovered, that it completly ignores all defined analog inputs. I've checked that in Tuner Studio with correctly defined AUX0 (to analog A0) and AUX1 (to analog A1 or others) and visible gauges on the dash, which don't move at all, when I apply voltage to PA0 and PA1 (or others accordingly).

So that might be the main problem.

VitorBoss, 2021-02-09:
I'll try to explain better this time, on ini there is a list of pins from 3 to 53, anything above that is treated by speeduino as analog channels because Mega2560 only have 53 IO pins and 16 analog ones, for STM32 it isn't true, for F407 there is 73 IO pins including 16 analog ones and the code is absolutely the same, for [F407 PB1](https://github.com/stm32duino/Arduino_Core_STM32/blob/master/variants/BLACK_F407XX/variant.h#L43) is pin 57 and isn't listed on the INI.

Any particular reason why you can't use the default pin for baro?

TrinomCZ, 2021-02-09:
Ah, I see. So the right input for PB1 should be A13. And I can confirm, that it works.
Thank you very much!

Closed 2021-02-10.

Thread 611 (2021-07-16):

BMP280

emretunali, 2021-07-16:
Hi,

Can we use an advanced barometric sensor like bmp280 instead of mpx?

VitorBoss, 2021-07-16:
The datasheet have code samples for the measurement in float and integer, speeduino only use integers. The SPI isn't possible due some boards use some SPI pins for other stuff, but it can be done for ARM variants of code, for AVR you can do it using I²C.

I don't see a problem with including that option, @noisymime opinion can be different, but you may do the code itself or ask for someone to do it for you if you want to play with it as this is very unlikely most users would use.

emretunali, 2021-07-16:
I'll code and test it myself. @noisymime  can add it to the new version if he sees fit.

noisymime, 2021-07-16:
Happy to look at it provided the code is neat and sane, though I don't believe there is any inherent advantage of a sensor such as this over the MPX or AD234. Given it's onboard, the baro sensor really has no issues with noise or ground offset, but happy to look at including it.

I would recommend using SPI over I2C as the latter can cause issues with the timers.

Also worth noting is that this sensor is not automotive rated.

emretunali, 2021-07-16:
bmp280 just wanted to give an example.  Nxp company's FXPS7115D4 automotive digital barometric sensor can be used.  It is newer technology and more affordable than the Mpx series.  Do you want to use SPI or i2c? @noisymime

noisymime, 2021-07-18:
SPI would be preferable. Like I said, no issues with this coming in, but other than widening the range of usable hardware I don't see there being any actual advantage for these sensors. They're all the same capacitive to voltage type sensors, the only difference with these ones is that they include the ADC onboard with a digital interface.

Closed 2021-09-21.

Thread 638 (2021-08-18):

feature request: PWM IDLE Duty Cycle Multiplier

choyr, 2021-08-18:
In my Honda B20 with a 500Hz IACV, a value of 1% has a change of about 150 rpm which is too coarse. Current setting is only 88-89%, with additional 4% from idle up. If possible to add a multiplier (ex. 100% is no change, and 10% is 10% of the final Duty Cycle) to have a better resolution and control.
Thanks
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

shiznit304, 2021-08-21:
did you add a flyback diode across your IAC

shiznit304, 2021-08-22:
I had the same issue with my NB1 Miata. You just need to solder in a diode across the 12v and ground wires in a certain way. That brought my pwm from the 86-89 range down to 20 - 60 range. It also reduced the audible buzzing noise

choyr, 2021-08-22:
Alright. Let me test it, because i did not put a flyback diode.
    On Sunday, August 22, 2021, 07:57:21 PM GMT+4, shiznit304 ***@***.***> wrote:

I had the same issue with my NB1 Miata. You just need to solder in a diode across the 12v and ground wires in a certain way. That brought my pwm from the 86-89 range down to 20 - 60 range. It also reduced the audible buzzing noise

—
You are receiving this because you authored the thread.
Reply to this email directly, view it on GitHub, or unsubscribe.
Triage notifications on the go with GitHub Mobile for iOS or Android.

Closed 2024-03-15.

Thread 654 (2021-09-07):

Conditional Rule references Incorrect

morrisman1, 2021-09-07:
We have been trying to solve why my rules wouldn't work and came across the following issues:

1)
When you create an AUX input under the accessories menu, the numbering starts from 0, and counts up from there.
In the available rule condition inputs, the list starts at Aux 1, however this actually references the Aux 0 input. The whole aux list is out by one position

2)
When you select from the list of conditions for the programmable outputs in Tunerstudio, at the point of VVT1 angle, the list goes out of sync by one position. For example to have a logic switching on WMI Tank Empty, you have to select the item above it on the list. A friend has explained it in the way that VVT1Angle is a 2-byte item, and the next item has the offset correct in main controller.ini, however in the list when you select the condition, it looks up 94 instead of 95, and puts the list out of sync.

I apologize that I'm not able detail much in relation to the code itself, I do not know the language. I hope the photos he sent me are useful.

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

Afroboltski, 2021-09-08:
After some further digging (I was the one who generated the initial screenshots above), I have discovered the problem lies mostly in the .ini file. I've attached a "fixed" version, but the only changes are the defs near the top:

`    #define fullStatus_def_1= "seconds", "status bits", "Engine status", "syncLossCounter", "MAP (Kpa)", "INVALID", "IAT / MAT", "coolant", "batCorrection", "battery voltage x10", "O2", "egoCorrection", "iatCorrection", "wueCorrection", "RPM", "INVALID", "AEamount/2", "GammaE", "INVALID", "VE1", "VE2", "AFR Target", "TPS DOT", "Advance", "TPS", "loopsPerSecond", "INVALID", "free RAM", "INVALID", "boostTarget/2", "Boost duty", "spark bits"

    #define fullStatus_def_2= "RPM DOT", "INVALID", "ethanolPct", "flexCorrection", "flexIgnCorrection", "idle Load", "testOutputs", "O2_2", "baro", "Aux in 0", "INVALID", "Aux in 1", "INVALID", "Aux in 2", "INVALID", "Aux in 3", "INVALID", "Aux in 4", "INVALID", "Aux in 5", "INVALID", "Aux in 6", "INVALID", "Aux in 7", "INVALID", "Aux in 8", "INVALID", "Aux in 9", "INVALID", "Aux in 10", "INVALID", "Aux in 11"

    #define fullStatus_def_3= "INVALID", "Aux in 12", "INVALID", "Aux in 13", "INVALID", "Aux in 14", "INVALID", "Aux in 15", "INVALID", "TPS ADC", "Error code", "Pulsewidth 1", "INVALID", "Pulsewidth 2", "INVALID", "Pulsewidth 3", "INVALID", "Pulsewidth 4", "INVALID", "status bits 3", "engineProtectStatus", "Fuel load", "INVALID", "Ignition load", "INVALID", "dwell", "INVALID", "idle C.L. target", "MAP DOT", "VVT1 Angle", "INVALID", "VVT1 Target"

    #define fullStatus_def_4= "VVT1 duty", "flexBoostCorrection", "INVALID", "baro correction", "Current VE", "ASE Value", "vss", "INVALID", "Gear", "Fuel Pressure", "Oil Pressure", "WMI duty", "WMI empty", "VVT2 angle", "INVALID", "VVT2 target", "VVT2 duty", "outputs status", "Fuel temp", "Fuel temp correction", "Advance 1", "Advance 2", "SD status", "running seconds x10", "INVALID", "Rule 1", "Rule 2", "Rule 3", "Rule 4", "Rule 5", "Rule 6", "Rule 7"

    #define fullStatus_def_5= "Rule 8", "INVALID", "INVALID", "INVALID", "INVALID", "INVALID", "INVALID", "INVALID", "INVALID", "INVALID", "INVALID", "INVALID", "INVALID", "INVALID", "INVALID", "INVALID", "INVALID", "INVALID", "INVALID", "INVALID", "INVALID", "INVALID", "INVALID", "INVALID", "INVALID", "INVALID", "INVALID", "INVALID", "INVALID", "INVALID", "INVALID", "INVALID"

    #define fullStatus_def_6= "INVALID", "INVALID", "INVALID", "INVALID", "INVALID", "INVALID", "INVALID", "INVALID", "INVALID", "INVALID", "INVALID", "INVALID", "INVALID", "INVALID", "INVALID", "INVALID", "INVALID", "INVALID", "INVALID", "INVALID", "INVALID", "INVALID", "INVALID", "INVALID", "INVALID", "INVALID", "INVALID", "INVALID", "INVALID", "INVALID", "INVALID", "INVALID"

    #define fullStatus_def_7= "INVALID", "INVALID", "INVALID", "INVALID", "INVALID", "INVALID", "INVALID", "INVALID", "INVALID", "INVALID", "INVALID", "INVALID", "INVALID", "INVALID", "INVALID", "INVALID", "INVALID", "INVALID", "INVALID", "INVALID", "INVALID", "INVALID", "INVALID", "INVALID", "INVALID", "INVALID", "INVALID", "INVALID", "INVALID", "INVALID", "INVALID", "INVALID"`
(Generated with a script to prevent typos, but let me know if I've missed any special cases)

The key thing here being that `"VVT1 Angle", "INVALID"` did not have the "INVALID" placeholder that allows the `byteNum` parameter to match up with what the firmware expects (in the `getStatusEntry(uint16_t byteNum)` method). I believe there were a few more missing after this entry too.

Additionally I've renamed the Aux. inputs so they go from 0 - 15 (as they are in TS),  instead of 1 - 16 (fixes the off-by-one error with the Aux. outputs).

Further, the `fsIntIndex` static EEPROM array in `globals.ino` (line 124) has a typo and is missing an entry. It should be:

`const byte PROGMEM fsIntIndex[] = { 4, 14, 17, 25, 27, 32, 41, 43, 45, 47, 49, 51, 53, 55, 57, 59, 61, 63, 65, 67, 69, 71, 75, 77, 79, 81, 85, 87, 89, 93, 97, 102, 109, 119 };`

i.e., 190 changed to 109, and 119 added. Can someone with write access please fix? :)

Cheers
Lance

[speeduino-fixed-08.09.2021.ini.txt](https://github.com/noisymime/speeduino/files/7127543/speeduino-fixed-08.09.2021.ini.txt)

Closed 2021-09-14.

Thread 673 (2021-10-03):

Aux Inputs Not Working

Corey-Harding, 2021-10-03:
I am unable to get aux inputs working as expected using the latest ini file and compiling the latest firmware (1d3a30ab4c08b146dd92ea21c55c9f138f808be8).  I have also applied fix #655 and no difference.  I first noticed this issue when trying to test PR #586.   In regards to #654 the inputs as listed under programmable outputs still start at 1 instead of 0 when using the [current ini file](https://raw.githubusercontent.com/noisymime/speeduino/master/reference/speeduino.ini), this is fixed in my ini file but still does not work as expected.  I submitted my updated ini as PR #676

There is one sequence I can run through to get the inputs to behave as expected which I will post below but the problem is back as soon as I power cycle and the input is unresponsive again.

A8 is hooked up to my ac switch and always works with idle up setting to increase and decrease idle but the two programmable outputs relying on a8 as an input to turn on compressor and fan only work when I follow the sequence below.

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

Attaching images of my settings and ini file/relevant info

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

shiznit304, 2021-10-03:
This is the fork I currently run in my 2000 Miata, feel free to give it a try. My aux inputs work fine. https://github.com/shiznit304/speeduino/commits/mycar5
It's the main branch from August 20, 2020 plus a few PRs such as #608 #549 #586 #607 #649 and one PR i haven't published yet for idle up with closed loop

Afroboltski, 2021-10-03:
Ah ha. I see the problem. https://github.com/noisymime/speeduino/issues/654 was closed and "fixed" but whoever merged it only applied half my fix - Aux in1-16 should be Aux in 0-15 in the fullStatus defs at the top.

github-account-0, 2021-10-03:
> Ah ha. I see the problem. #654 was closed and "fixed" but whoever merged it only applied half my fix - Aux in1-16 should be Aux in 0-15 in the fullStatus defs at the top.

I tried simply renaming them and it didnt work, is my PR #675 wrong then and there is more to it?

github-account-0, 2021-10-03:
I was able to workaround this bug by modifying the following line in globals.h
https://github.com/noisymime/speeduino/blob/93de5eecda3bc288394da73b998331080694e877/speeduino/globals.h#L607

to read

`#define pinIsUsed(pin)      ( pinIsInjector((pin)) || pinIsIgnition((pin)) || pinIsSensor((pin)) ) //|| pinIsOutput((pin)) || pinIsReserved((pin)) )`

github-account-0, 2021-10-03:
Im confused because A8 is free in the init I even commented the spare1 out and it had no effect
```

    case 41:
    #ifndef SMALL_FLASH_MODE //No support for bluepill here anyway
      //Pin mappings as per the UA4C shield
      pinInjector1 = 8; //Output pin injector 1 is on
      pinInjector2 = 7; //Output pin injector 2 is on
      pinInjector3 = 6; //Output pin injector 3 is on
      pinInjector4 = 5; //Output pin injector 4 is on
      pinInjector5 = 45; //Output pin injector 5 is on PLACEHOLDER value for now
      pinCoil1 = 35; //Pin for coil 1
      pinCoil2 = 36; //Pin for coil 2
      pinCoil3 = 33; //Pin for coil 3
      pinCoil4 = 34; //Pin for coil 4
      pinCoil5 = 44; //Pin for coil 5 PLACEHOLDER value for now
      pinTrigger = 19; //The CAS pin
      pinTrigger2 = 18; //The Cam Sensor pin
      pinTrigger3 = 3; //The Cam sensor 2 pin
      pinFlex = 20; // Flex sensor
      pinTPS = A3; //TPS input pin
      pinMAP = A0; //MAP sensor pin
      pinBaro = A7; //Baro sensor pin
      pinIAT = A5; //IAT sensor pin
      pinCLT = A4; //CLS sensor pin
      pinO2 = A1; //O2 Sensor pin
      pinO2_2 = A9; //O2 sensor pin (second sensor)
      pinBat = A2; //Battery reference voltage pin
      pinSpareTemp1 = A8; //spare Analog input 1
      pinLaunch = 37; //Can be overwritten below
      pinDisplayReset = 48; // OLED reset pin PLACEHOLDER value for now
      pinTachOut = 22; //Tacho output pin
      pinIdle1 = 9; //Single wire idle control
      pinIdle2 = 10; //2 wire idle control
      pinFuelPump = 23; //Fuel pump output
      pinVVT_1 = 11; //Default VVT output
      pinVVT_2 = 48; //Default VVT2 output
      pinStepperDir = 32; //Direction pin  for DRV8825 driver
      pinStepperStep = 31; //Step pin for DRV8825 driver
      pinStepperEnable = 30; //Enable pin for DRV8825 driver
      pinBoost = 12; //Boost control
      pinSpareLOut1 = 26; //low current output spare1
      pinSpareLOut2 = 27; //low current output spare2
      pinSpareLOut3 = 28; //low current output spare3
      pinSpareLOut4 = 29; //low current output spare4
      pinFan = 24; //Pin for the fan output
      pinResetControl = 46; //Reset control output PLACEHOLDER value for now
    #endif
      break;
```

It is one of these outputs but everything shows board defaults listed above

`#define pinIsOutput(pin)    ( ((pin) == pinFuelPump) || ((pin) == pinFan) || ((pin) == pinVVT_1) || ((pin) == pinVVT_2) || ((pin) == pinBoost) || ((pin) == pinIdle1) || ((pin) == pinIdle2) || ((pin) == pinTachOut) )
`

I cant find A8 being used when looking through menus or at io summary  besides my idle up setting.

github-account-0, 2021-10-03:
Is idle up set as pinIdle1 or pinIdle2?

Is that why it doesnt work?

shiznit304, 2021-10-03:
my guess is that it uses pinIdle 1 in a 2 wire idle controller, and both
pin idles in a 3 wire controller?

On Sun, Oct 3, 2021 at 6:19 PM github-account-0 ***@***.***>
wrote:

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

Afroboltski, 2021-10-04:
I think half the problem here is that the pin number for various functions is still written to the EEPROM from TS, even if the function is disabled. For example you set idle valve to pin X, then disable idle control, pin X is still being written to the EEPROM, so the firmware still believes it's used?

You'll see in my A/C compressor control implementation (https://github.com/noisymime/speeduino/pull/665), I interlocked the pin assignment with the A/C enable status, but no other feature seems to do this

shiznit304, 2021-10-04:
have you looked into #549 ? I didn't need it to make it work but I did need it to use idlePin2 for other functions other than for idle control. In fact, i use idlePin2 to play euroBeat when TPS > 50% 😂

github-account-0, 2021-10-04:
I tried out #549 it didnt work for me in this case

github-account-0, 2021-10-04:
If anyone else has this issue and needs a WORKAROUND(perhaps not a proper solution) they can try my fork and ini file that has #655, #676, and reverts part of #398

https://github.com/github-account-0/speeduino

choyr, 2022-01-14:
tried it today with UA4C, it is not working for Aux input gauges, but if I use it for fuel/oil pressure, it works

Afroboltski, 2022-01-16:
Yup it's still wrong in the INI file in the current release, and the off-by-one error still exists on line 100 for sensors.ino

Corey-Harding, 2022-01-16:
Check PR #745

Corey-Harding, 2022-01-17:
> tried it today with UA4C, it is not working for Aux input gauges, but if I use it for fuel/oil pressure, it works

What did you try?

choyr, 2022-01-17:
I used A8 to A13 and tried aux input gauges and they are not responding. However, if i use for example A8 as fuel pressure, it works same as A10 as oil pressure. Maybe i did something wrong, i will check again later
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
Corey-Harding, 2022-01-24:
Here is the current tune

[2022-01-23_19.29.17.zip](https://github.com/noisymime/speeduino/files/7921821/2022-01-23_19.29.17.zip)

Corey-Harding, 2022-01-24:
If there was an IdleUpActive True/False status under programmable output options as my trigger instead of me having to use Aux 0 Analog Input A8 I feel like it would solve my issue.

shiznit304, 2022-01-24:
Do what I did, wire your ac input into an op amp, it’ll turn your signal
into an on/off input

On Sun, Jan 23, 2022 at 6:39 PM Corey-Harding ***@***.***>
wrote:

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

Corey-Harding, 2022-01-24:
Im just concerned if I resolder the wire to a different pin or do as ypu say that I still have to use that pin for idle up so I think adding idleUpActive as a trigger instead of reading the 0-1023 value of A8 is a good option. Im not sure how to do that yet though.

shiznit304, 2022-01-24:
I used to use analog input as an AC trigger but unfortunately The voltage
level from the AC switch does not go low enough to trigger a digital low
signal. It wouldn’t go below the threshold, so instead I added an app amp
to turn the 12 V to 3 volt signal into a 0/5 V signal for digital input

On Sun, Jan 23, 2022 at 8:40 PM Corey-Harding ***@***.***>
wrote:

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

Afroboltski, 2022-01-24:
Just wait until my AC control is merged ;)

[https://github.com/noisymime/speeduino/pull/665](url)

shiznit304, 2022-01-24:
You don’t have idle rpm target adjustment in there. I recommend adding that
feature

On Sun, Jan 23, 2022 at 8:48 PM Afroboltski ***@***.***>
wrote:

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

Corey-Harding, 2022-01-24:
Your PR cant automatically merge or I would test it.  Might check into it still though if I have time to see what is conflicting.

Corey-Harding, 2022-01-24:
Also @Afroboltski i was told not to do +1 on auxinpina here
https://github.com/noisymime/speeduino/pull/676

Afroboltski, 2022-01-24:
the +1 is ONLY for the digital pins, the analogs were OK I believe, from memory

Corey-Harding, 2022-01-24:
You have it in your pr to do +1 on analog as well.

Also you dont have an output selection for condensor fan. I have two outputs i need. One for ac relay and one for condensor fan.

Afroboltski, 2022-01-24:
> Your #665 PR cant automatically merge or I would test it. Might check into it still though if I have time to see what is conflicting.

Yeah it's a bit stale, I'm planning on updating it (just re-writing it will be easier actually) well before the next FW release

> You don’t have idle rpm target adjustment in there. I recommend adding that feature

OK, consider it done!

Corey-Harding, 2022-01-24:
See comment above i feel like we posted at the same time and you may miss it

Afroboltski, 2022-01-24:
> You have it in your pr to do +1 on analog as well.
>
> Also you dont have an output selection for condensor fan. I have two outputs i need. One for ac relay and one for condensor fan.

Ahh. I see the confusion.

Looking at #676, I agreed with pazi88, who pointed out that adding the +1 to the auxinpinaline was incorrect.

And in #655 I never mentioned auxinpina.

Looks like I chucked it into the Air Conditioning PR (#665) by accident! Sorry about that.

Corey-Harding, 2022-01-24:
Also will you add an additional ac condensor fan output field to your pr for those like me where it isnt the same as the relay

Afroboltski, 2022-01-24:
> Also will you add an additional ac condensor fan output field to your pr for those like me where it isnt the same as the relay

Yes, in fact I already did! As I mentioned in the 13th of October comment 😎

Corey-Harding, 2022-01-24:
Thats awesome news!  Forgive me if I had read it before I had forgotten.

Corey-Harding, 2022-03-16:
I think my aux inputs are working(I only have one on A8) and its my combination of settings that won't work.  I was able to unrevert the pinisused related commit and switch my idle up output to a digital pin and setup same digital pin to an input and now the current firmware works the same as a few weeks ago and ac cycles on and off a few seconds at a time.

I am unsure if the minimum time setting in progout is working though, at least not with my settings as I tried to use that to compensate and it didnt work.

I am also starting to wonder if idle initiliase is triggering every few seconds and reinitialising my pins or another initialise event is occuring.  It seems idlue up steps does not work in ol+cl so not sure what else is missing as well.

Afroboltski, 2022-07-09:
Dredging up the past here,

Does this fix this issue? #887

noisymime, 2024-02-05:
Closing as this appears to have been resolved quite some time ago

Closed 2024-02-05.

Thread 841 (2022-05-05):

BUG (stm32): Comms/startup issue Master branch

sbtoonz, 2022-05-05:
Processor: STM32F407VGT

Symptom:
When plugging board into power it fails to boot.

Steps to replicate:
Compile master d2b9612409bff3b54a172f77014e4d6ca621db4e
Flash to stm32
unplug board

plug board in
board fails to boot speeduino

sbtoonz, 2022-05-05:
commenting out SDCard logging resolved this

most likely its searching SPI on boot and failing to find the sdcard logger

noisymime, 2022-05-05:
I will test this over the next few days, but issue is (at worst) limited to stm32 only.
When you're seeing this, is the tune on the board (If there is one) set to use SD logging?

sbtoonz, 2022-05-05:
The tune was set to sd logger by default once loading the new INI into tuner studio (at least I am supposing so as this didn't exist in prior release version and that's what I was running prior to today) and today once I finally got connection made (by resetting multiple times) I could see the "Sdcard ready" green on the dash

That led me to comment out the define for the sd logging in stm32 and attempt to repeat the connection error

I could not repeat once commenting out

So this issue would present itself upon updating if the board was not provisioned for SD unless there's a way to default it false without undefining (I'm not sure if defines can be applied at runtime in this environment)

pazi88, 2022-05-05:
I can see this issue too. Most of the time it fails to boot if SD-card logging feature is compiled and even when the board boots, it takes really long time. I did not have this issue when I added the SD-card logging for STM32, so it's new thing. Need to investigate.

pazi88, 2022-05-05:
And yes if SD logging is commented out, the board boots up just fine. But I can't seem to find my ST-link dongle anywhere, so investigating this happens when I found it. Disabling SD-logging from TS-doesn't seem to help.

transi01, 2022-05-05:
where to comment out the SD logging?

pazi88, 2022-05-05:
> where to comment out the SD logging?

[bo](https://github.com/pazi88/speeduino/blob/dcb8fa009f6f99f2b88747cb6f45f653943145d2/speeduino/board_stm32_official.h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)

transi01, 2022-05-05:
Thanx :-)

pazi88, 2022-05-05:
Ok, I'm starting to get hang of this. It's actually the RTC that is causing the problem. If I have the RTC battery on the board (and RTC time/date set in TS) it boots up normally/immediately. If I don't have RTC battery on the board, it hangs up on boot or doesn't boot at all. This makes sense because the date/time is used for the log files and if there is no battery, the RTC isn't running on the board. Without SD-logging the RTC on STM32 wasn't used at all. This of course need to be fixed, because missing/empty RTC battery should not cause problems for booting up.

pazi88, 2022-05-25:
Yes problem is still there. I have the problem somewhat narrowed down. But no fix yet, although you can prevent it by adding rtc battery. If I don't come up fix before next release, josh needs to comment out that line in master.

pazi88, 2022-05-25:
> > Yes problem is still there. I have the problem somewhat narrowed down. But no fix yet, although you can prevent it by adding rtc battery. If I don't come up fix before next release, josh needs to comment out that line in master.
>
> setting this define enables by default correct? This option can still be enabled via project settings in that use case if I am not mistaken?

Nope, it's build flag. SD-logging doesn't work at all if you disable it for building.

Disabling SD-logging in TS, doesn't really help this issue because the code does RTC/SD init anyways.

sbtoonz, 2022-05-26:
https://www.aliexpress.com/item/3256801471796407.html?spm=a2g0o.order_list.0.0.46d81802iJ8Wrx

just tried latest master with this board which has RTC crystal and SDCard slot provisioned

Failed to boot

Closed 2022-06-27.

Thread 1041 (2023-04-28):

Current master fails to build in Arduino.ide - it fails to handle extension .inl

mike501, 2023-04-28:
Current master has an #include "schedule_calcs.inl" in schedule_calcs.h. This fails on arduino IDE as it doesn't seem able to include a .inl file. Code appears to have been added on 6/3/23 as part of a general piece of work to improve unit tests - pull request #1010

noisymime, 2023-04-29:
Fixed in #1042

Closed 2023-04-29.

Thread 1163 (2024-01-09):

OddSquirt not working on low RPM`s

RempageR1, 2024-01-09:
Hi,

I have a Vmax that will run it`s injectors close to the cylinder head as possible. I do this by setting the injector degrees to the oddfire degrees as shown below:

channel2InjDegrees = configPage2.oddfire2;
channel3InjDegrees = configPage2.oddfire3;
channel4InjDegrees = configPage2.oddfire4;

And this works just fine, until you get under 450 RPM. Then, injectors 3 and 4 go nuts and fire about twice as much as 1 and 2 do. Above 450 RPM everything is well.

In my setup, channel 2 is at 180 degrees, which is the same as even fire, so that explains why 1 and 2 are fine. 3 is at 430 and 4 is at 540.

Is there any way to fix the oddSquirt behavior at low RPM? Cranking is set to 400, so it`s not that.

Thank you.

RempageR1, 2024-01-10:
Connected the scope today and the issue is also there on channels 1 and 2 (albeit less). So this is a generic issue on low-RPM fuel delivery.

RempageR1, 2024-01-11:
Did some more testing, and you can see the scheduler status is different for output 3 is different at the time I see the issue. The two Serial.print() commands were added to all 4 injectors:

-----------------------------------------------
#if INJ_CHANNELS >= 1
      if( (maxInjOutputs >= 1) && (currentStatus.PW1 >= inj_opentime_uS) && (BIT_CHECK(fuelChannelsOn, INJ1_CMD_BIT)) )
      {
        uint32_t timeOut = calculateInjectorTimeout(fuelSchedule1, channel1InjDegrees, injector1StartAngle, crankAngle);
        if (timeOut>0U)
        {
Serial.print("1 ");
Serial.println(fuelSchedule1.Status);
        setFuelSchedule(fuelSchedule1,
                      timeOut,
                      (unsigned long)currentStatus.PW1
                      );
        }
      }
#endif
-----------------------------------------------

And the one that bliks twice is #3.
1 0
2 0
3 1
4 0
1 0
2 0
3 1
4 0
1 0
2 0
3 1
4 0

I really hope there is someone that can work with this because it`s above my coding stills. You can reproduce this in the latest dev release and 60-2 trigger wheel using even-fire. Then try some RPM`s below 400 and you`ll run into the same issue.

adbancroft, 2024-01-11:
> You can reproduce this in the latest dev release and 60-2 trigger wheel using even-fire. Then try some RPMs below 400

On a Mega, I setup 60-2 missing tooth crank speed wheel, used the oddfire settings you describe (0, 180, 430, 540), cranking RPM at 200 and used Ardustim to feed a 350 RPM signal. A logic analyzer hooked to the Mega shows a nice even set of injector traces:
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

Latest master.

What setting am I missing to repro?'
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

RempageR1, 2024-01-11:
It only happens at very specific RPM`s like 348. But that number is just a guess. I can get you the exact number tomorrow and I`ll use your exact settings then. I use the Teensy3.5 so that might be a difference. This is what my scope shows, Ignite 3 vs Fuel 3:

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

noisymime, 2024-01-11:
Can you post your full tune please.

I cannot reproduce this at a quick try, testing between 250 and 500 RPM I get results as expected on all 4 outputs. This is testing with a mega2560 though as I didn't have the Teensy set up. It is possible that this is someething to do with the lower overall timer timeout on the Teensy, but I can't see why that would only impact a certain channel and is getting checked for anyway, so that seems unlikely.

I'll try with your full tune though.

RempageR1, 2024-01-12:
[2024-01-12_15.57.19.zip](https://github.com/noisymime/speeduino/files/13921141/2024-01-12_15.57.19.zip)

Above is the standard tune I use to reproduce this. I see the issue at 256 RPM on the Teensy. I`ve also dusted off my old mega2560 and indeed the issue isn't there. If you need me to test something with the Teensy I`d be happy to help...

adbancroft, 2024-01-12:
You are using VMax, right?

I noticed this in `triggerPri_Vmax()`:
  `setFilter((curGap/1.75));//Angle to this tooth is 70, next is in 40, compensating.`

`curGap` is `unsigned long` & the `setFilter` parameter is also `unsigned long`.....so this doesn't do what the author thinks it's doing.

Possible issue, though the code has been there for almost 2 years.

adbancroft, 2024-01-12:
> As I`m not really a coder, perhaps you can tell me why this is a problem so I can fix it.

I *thought* it would apply integer division, but after writing a [quick test](https://godbolt.org/z/qxn1fz6P6), it looks like it might be doing what's expected after all - at least on a desktop compiler, the divisor is promoted to double, followed by a floating point divide and then truncation to unsigned long. Which is probably good enough

It will be horribly slow on anything that doesn't have an FPU though.

RempageR1, 2024-01-13:
Thank you for speeding up this code :).

If there is anything I can test for the timing issue on the Teensy i`d be happy to help. Please not it only occurs in the injection channels, and not the ignition channels.

giovannni97, 2024-01-17:
Hi, I also am using the Vmax decoder but in order to really get it working i needed to change the MAX9924 VR interface from A2 mode to C --> Our "large tooth" is otherwise often misinterpreted because it trigger on the zero crossing which might be just noise and not the falling edge of the tooth.

mike501, 2024-01-17:
I've seen this issue mentioned a number of times with the max VR
conditioner. Do have a rough rule of thumb when it becomes an issue that
can be added to the wiki as a general guide, eg trigger wheels with less
than x teeth etc etc

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

giovannni97, 2024-01-17:
The MAX VR conditioner "power" lies in its A2 mode which is essentially an automagically adjustable hysteresis filter so that each positive trigger is recognized if it is at least 1/3 of the previous peak amplitude. The negative peak tho is basically ignored since when the signal goes to zero even for an instant the output goes low, no filter added.
This is generally a non problem since 99% of trigger wheels have fixed-width teeth and the position is given trough gaps --> the system only need to care about either the start or the end of a tooth, not togheder in the same application.
My Yamaha XTZ750 and @RempageR1 though have differently sized teeth and the position is obtained by looking at each lenght --> we need to look at the start (positive pulse) and end (negative pulse) on each tooth.
The MAX VR on A2 mode will basically be always spot on for the positive trigger but almost always mess up on the negative.
The barebone method is to add a low freq LP filter (high R and C on input of MAX VR) to hope that the residual voltage on the CAP will prevent the signal from crossing to zero after the poisitive pulse until the negative (end of tooth) pulse happen.

The mode C which I adopted loses the automatic filter on input (now is fixed value for the HYS threshold) but it is now symmetrical so that I can have a reasonable RC on input and see both rising and falling edge when needed.

Sorry for the long post but it is a complex issue not fully discussed given the limited times it is truly needed

RempageR1, 2024-02-12:
I`ll close this one and open one with proper (new) information. This is happening on both Teensy 3.5 and my new 4.1 setup. It happens on all injection channels, all modes not only oddifre but also in paired or semi-sequential mode.

Closed 2024-02-12.

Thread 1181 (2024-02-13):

Dual injections on low RPM with Teensy 3.5 and 4.1

RempageR1, 2024-02-13:
Hi,

I am opening this issue as a continuation of #1163. There I thought there was an issue with oddsquirt but the issue is much bigger than that.

In any mode (paired, semi-sequential, sequential) there are multiple injections below a certain RPM. With Teensy3.5, the issue occurs sporadically at certain RPM`s and goes away around 450 RPM.
I also tested it with a Dropbear-like unit with Teensy 4.1 and MC33810s which also works fine up to around 450 RPM. Then, channel 4 starts to behave strangely (dual injections) sequential mode followed by channel 3. A bit higher in the RPM, channel 2 also shows dual injections and around 1000RPM all four channels have dual injections. At 1080RPM, suddenly all injector channels start to behave as they should. This only affects the injectors, NOT the ignition.

On the mega2560 the issue isn’t there.

Attached are five pictures. Blue is the injector, yellow is ignition of cylinder 1 for reference.
1 shows channel 4 @ 543 RPM
2 shows channel 4 @ 940 RPM
3 shows channel 3 @ 940 RPM
4 shows channel 1 @ 940 RPM
5 shows channel 1 @ 1110 RPM.

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

And here is the current tune:
[CurrentTune.zip](https://github.com/noisymime/speeduino/files/14271528/CurrentTune.zip)

I`m running the latest dev version. I hope someone can have a look at this. If I need to test anything with the Teensy 3.5 or 4.1 please let me know.

RempageR1, 2024-02-15:
I did quite some testing with this one and came up with a workaround. It is not pretty and I am probaly fighting symptoms and not the root cause but perhaps it helps someone with the proper coding skills to identify the problem. Whenever I divide the timeout that is sent to the setFuelSchedule() function, the RPM`s where the issue occurs is divided by 2 as well. So if the issue occured at 1000 RPM, the timeout/2 makes it happen at 500, and no longer above. If I however divide the timeout too much, I am running into issues at the higher RPMs. The function below now has code that divides the timeout by 64 below 200RPM and divides by 8 below 1200RPM:

`
static inline uint32_t _calculateInjectorTimeout(const FuelSchedule &schedule, uint16_t openAngle, uint16_t crankAngle) {
  int16_t delta = openAngle - crankAngle;
  if (delta<0)
  {
    if ((schedule.Status == RUNNING) && (delta>-CRANK_ANGLE_MAX_INJ))
    {
      // Guarenteed to be >0
      delta = delta + CRANK_ANGLE_MAX_INJ;
    }
    else
    {
      return 0;
    }
  }
  if ( currentStatus.RPM < 200){
    return angleToTimeMicroSecPerDegree((uint16_t)delta)/64;
  }
  else if ( currentStatus.RPM < 1200){
    return angleToTimeMicroSecPerDegree((uint16_t)delta)/8;
  }
  else{
    return angleToTimeMicroSecPerDegree((uint16_t)delta);
  }

  //return angleToTimeMicroSecPerDegree((uint16_t)delta);
}
`

noisymime, 2024-02-15:
Suspect I can see the cause of this. Will test later today and get a fix out asap if it is that

noisymime, 2024-02-15:
Strangely I could not reproduce this at all on either T3.5 or T4.1. I'm assuming your testing has been with the latest code on master or was this with one of the older released versions?

I've pushed up a small change that aligns the logic fuel setting function exactly with the ignition one, though I would be surprised if this makes a difference. It also includes a small change on the T3.5 timeout value for safety.

Could you please try the current dev code with that change pushed and see if you get the same issue?

RempageR1, 2024-02-16:
Yes, I am testing with the latest version. I`ve pulled the latest version and tested on my teensy 4.1.

Be prepared to be surprised because it does fix the dual injections :). I`ll also try and see if it fixes it on the 3.5, after that I think we can close this one.

Last year I was very confused why the O2 was all over the place at idle, but dual injections might just be the reason why :)

Thank you for fixing this!

RempageR1, 2024-02-16:
Teensy 3.5 also works fine now. I`ll close this one. Thanks again!

noisymime, 2024-02-16:
Well I won't complain if that's resolved it, but it's certainly surprising. Were you using one of the recent pulls from master or something from last year?

RempageR1, 2024-02-17:
Hi noisymime, yes I was using the master, current version. Not something from last year. If it works, it works :).

RempageR1, 2024-02-24:
Spoke too soon. I tested with the Injector timing at 0, which worked flawlessly. However if you set them to 360 (or above 200), I get dual pulses all all injectors at certain RPM`s. So no not fixed I`m afraid...

RempageR1, 2024-03-10:
Well, I fixed the remaining issue for my setup. The calculateInjectorStartAngle does get the currentStatus.injAngle as an argument, but the calculateInjectorTimeout() doesn't. I think it is therefore misaligned. What I did for now is the following:

I added this to the speeduino.ino, so it uses the injector degrees (oddsquirt in my case) plus the injector close angles at the beginning of the timing routine. Therefore the correct channelXInjDegrees are used for both calculateInjectorStartAngle() and calculateInjectorTimeout();

      //***********************************************************************************************
      //BEGIN INJECTION TIMING
      currentStatus.injAngle = table2D_getValue(&injectorAngleTable, currentStatus.RPMdiv100);
      if(currentStatus.injAngle > uint16_t(CRANK_ANGLE_MAX_INJ)) { currentStatus.injAngle = uint16_t(CRANK_ANGLE_MAX_INJ); }
      unsigned int PWdivTimerPerDegree = timeToAngleDegPerMicroSec(currentStatus.PW1); //How many crank degrees the calculated PW will take at the current speed

      channel1InjDegrees = currentStatus.injAngle;
      channel2InjDegrees = configPage2.oddfire2 + currentStatus.injAngle;
      if (channel2InjDegrees >= (uint16_t)CRANK_ANGLE_MAX_INJ ){
        channel2InjDegrees = channel2InjDegrees - (uint16_t)CRANK_ANGLE_MAX_INJ;
      }
      channel3InjDegrees = configPage2.oddfire3 + currentStatus.injAngle;
      if (channel3InjDegrees >= (uint16_t)CRANK_ANGLE_MAX_INJ ){
        channel3InjDegrees = channel3InjDegrees - (uint16_t)CRANK_ANGLE_MAX_INJ;
      }
      channel4InjDegrees = configPage2.oddfire4 + currentStatus.injAngle;
      if (channel4InjDegrees >= (uint16_t)CRANK_ANGLE_MAX_INJ ){
        channel4InjDegrees = channel4InjDegrees - (uint16_t)CRANK_ANGLE_MAX_INJ;
      }

Then, I removed the injAngle from the calculateInjectorStartAngle routine (it is now unused):

     ////int16_t startAngle = (uint16_t)injAngle + (uint16_t)injChannelDegrees;
     int16_t startAngle = (uint16_t)injChannelDegrees;

Hope this helps. If it looks good, I could create a pull request for this. Thank you.

RempageR1, 2024-03-11:
Update: Yep it can be done simpler. The issue is indeed the fact that calculateInjectorTimeout() doesn't take the injAngle value into account. Below shows the old and new calculateInjectorTimeout() routine. I added the injAngle from the currentStatus to the equation and ensure we do not go over the max degrees (360/720). This should be a permanent fix that works for all setups (showing old and new):
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
noisymime, 2024-12-08:
Hmmm OK. I'll try those and see if I can reproduce what you're seeing. Thanks again for the testing.

adbancroft, 2024-12-09:
A couple of shots in the dark for you to try:

1. https://github.com/adbancroft/speeduino/tree/SCHD_7_optimize_FuelSchedule. Uses same basic scheduling algorithm as master, but has a few more checks in it.
2. https://github.com/adbancroft/speeduino/tree/OptimisePw. Uses a fuel scheduling algorithm based more in the time domain than angular (no change to ignition...yet).

YMMV, these haven't been seen by anyone but myself.

noisymime, 2024-12-10:
```
channel2InjDegrees = configPage2.oddfire2;
channel3InjDegrees = configPage2.oddfire3;
channel4InjDegrees = configPage2.oddfire4;
```

This looks like it should be something that is there by default. The oddfire timing currently only changes the ignition angles but it makes sense for them to apply to the injection angles as well.

> When setting 'injector characteristics' degrees around 142 and the RPM at 3677, channel 1 shows a lot of missed injections. If I then change the oddfire angle of cylinder 2 to 142 and set the 'injector characteristics' at 0, the issue moves to injector 2.

Hmmm even with the change you're mentioned added, I cannot seem to reproduce this at all. I've pushed 1 further small change up on that branch, but I don't think it will have any impact as I can't see this issue with or without it applied.

I've set it exactly as you've described and tried pulsewidths all the way from 2ms to 17ms and am not seeing issues on any injection channels. I'm testing 4 cylinder, sequential with a 12+1 dual wheel trigger arrangement. This is all on Teensy 4.1, I haven't tried 3.5 but I'd be surprised if it was different.

I'll keep having a play and see if I can get anything to show up.

noisymime, 2024-12-10:
Just FYI, I've created #1271 to add oddfire angles to the injection timing.

noisymime, 2024-12-11:
OK, I've pushed up a small change to the schedule rework branch that should fix this.

From my testing, there is roughly a 2 RPM 'window' for any given pulsewidth where this could theoretically occur, so unlikely but not impossible. With this last addition though I can no longer reproduce it under any conditions.

noisymime, 2024-12-11:
May have spoken too soon. New fix coming

noisymime, 2024-12-11:
OK, so turns out this wasn't a problem with the value being 0, it's when the injection start angle value is rapidly changing back and forth between 0 and `CRANK_ANGLE_MAX_INJ`.

This should be fixed now in the above mentioned branch

RempageR1, 2024-12-11:
> OK, so turns out this wasn't a problem with the value being 0, it's when the injection start angle value is rapidly changing back and forth between 0 and `CRANK_ANGLE_MAX_INJ`.
>
> This should be fixed now in the above mentioned branch

Yes! Indeed I tested it and it looks good now. Thank you for working in this issue. Great to have it resolved!

RempageR1, 2024-12-11:
> Since we're essentially juggling [modular arithmetic](https://en.wikipedia.org/wiki/Modular_arithmetic), we should limit injection angles to [0, CRANK_ANGLE_MAX_INJ**-1**], aka [0, CRANK_ANGLE_MAX_INJ). E.g. 0-719°. Same for ignition angles.
>
> That's what https://github.com/adbancroft/speeduino/tree/OptimisePw (mentioned above) does - not sure if it got tested by @RempageR1.

I suggest we wait to see if @noisymime finds this needs to be part of the main Speeduino code. If he does, I`d be happy to do some testing.

noisymime, 2024-12-11:
> Since we're essentially juggling [modular arithmetic](https://en.wikipedia.org/wiki/Modular_arithmetic), we should limit injection angles to [0, CRANK_ANGLE_MAX_INJ**-1**], aka [0, CRANK_ANGLE_MAX_INJ). E.g. 0-719°. Same for ignition angles.
>
> That's what https://github.com/adbancroft/speeduino/tree/OptimisePw (mentioned above) does - not sure if it got tested by @RempageR1.

I'll start having a look at these next week. To be honest this was a bigger problem to work through than I had expected, the deeper I dug the more things I found and it was quite time heavy to test. I'll clean up the branch as it is now and merge it and then start looking at larger changes to the whole scheduling system.

One thing I've (re)learned coming out of this is that there are a LOT of edge cases that need to be handled and that aren't always obvious or easy to test for. Need to have a think about how best to automate those as they were very time intensive to reproduce.

@RempageR1 Thanks for all your work in testing this!

Closed 2024-12-19.

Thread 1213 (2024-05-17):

202402 firmware VVT1 no reading and no duty aplied to solenoid.

h25r, 2024-05-17:
Hi!
Im running efi core4 from pazi88 github with no issues on firmware 202305
i updated to latest firmware and im having some problems
VVT1 sensor dont read any value, and no duty aplied to solenoid, closed or open loop dont make any difference.
I talked with more people with same issue
Also having problems reading CAN inputs and PWM fan output but maybe are caused by the changes on secondary serial.

[CurrentTune.zip](https://github.com/noisymime/speeduino/files/15358395/CurrentTune.zip)

dougsgh, 2024-05-26:
I'm having the same problem. First time build. I can't get any vvt1 or 2 output happening in open or closed loop. Tried multiple settings. I'll try older firmware.

noisymime, 2024-05-26:
Are you able to provide a log in addition to your tune?

noisymime, 2024-05-26:
This looks to have been a change in the way the secondary tooth is handled when the `Poll` option is selected.

The Poll option was never specifically intended to be usable with closed loop VVT, but I can reinstate the same behaviour as was there previously.

This doesn't impact any of the other secondary VVT patterns

noisymime, 2024-05-26:
This should be resolved now.

If you're able to try the Master firmware version (Available in SpeedyLoader at the bottom of the list) and confirm, that would be good.

dougsgh, 2024-05-27:
Thanks noisymime!

Should I be downloading a new ini file from somewhere? I clicked connect anyway.

So with the latest 'master' firmware loaded in, I am now able to see cam angles on both cams, however I am still not able to get any vvt1 or 2 output happening in open or closed loop. On startup, no cam angle is shown until after a composite log. The cam angle does not appear to change when manually actuating the VVT solenoid (which almost stalls the engine - so is definitely changing)

A few project details and some plot thickeners...
This is for a Y62 patrol with the later model v8 in the earlier model, series 1. The S1 has vvt on inlet cams only, the later model engine, which I now have running here (Perth, WA) has vvt on exhaust cams too. The original ecu is running everything apart from the exhaust VVT. I have a 0.4 board running piggyback off the stock crank sensor, and independently connected to both exhaust cam position and vvt solenoids.  I dont have MAP or coolant temp connected as yet which might upset things.
The other thing that might upset things is the stock triggers arent supported, crank is 36-2-2, 180 degrees apart, you will notice I have the tune set to 18-2 (seems to work and sync, obviously rpm is double, but not serious for VVT only). The other non supported piece is the stock cams are 4T. Running the crank as half a crank, it would only be a 2T, although, I realise still not supported. (I was hoping to get running and then explore some firmware tweaks).

This is becoming a common engine swap in Australia due age of S1 and availability/cost of s1 engines vs s5 engines. The majority are going down the route of s1 fixed exhaust cam sprocket swap, but I felt the need for some discovery.

In essence, I realise there are probably better guinnea pigs out there, and this should be a new feature request with a healthy donation to the cause which I am happy to do!
[VK56 VVT.zip](https://github.com/noisymime/speeduino/files/15453510/VK56.VVT.zip)

dougsgh, 2024-05-27:
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

h25r, 2024-05-27:
> This should be resolved now.
>
> If you're able to try the Master firmware version (Available in SpeedyLoader at the bottom of the list) and confirm, that would be good.
[TestMaster.zip](https://github.com/noisymime/speeduino/files/15461913/TestMaster.zip)

Not working for me.
Add log and tune.

noisymime, 2024-05-28:
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

OK, that (and your pictures) clears things up a bit.

First off that trigger arrangement is never going to work with the `Poll` secondary type. Poll is designed for use with things like a 'half moon' cam pattern where the level of the cam reading changes at tooth #1

In your case I'd say you should be using the 'Single tooth cam' option, however that 4T tooth on the cam isn't going to work for closed loop VVT either.

Ultimately I think it's going to need a proper decoder for this setup as trying to band-aid it with patterns that don't really fit isn't ideal.

I'll see if I can dig up any proper timing charts for this pattern.

dougsgh, 2024-05-28:
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

Appreciated, thanks!

I am a little confused however, the trigger setting I have is set to single tooth, am I missing something?

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

In regards to decoders, one stumbling block for this engine is sync must ultimately be determined by the stock ecu using the intake cam 1 and 2 (not connected to speeduino here) patterns which are 4+1+1+0+0 and 4+0+0+1+1 for the respective banks. The crank being 36-2-2 (16 T - 2, 16 - 2) and the 4T exhaust cams arent going to determine "sync". Given that I dont need fuel or spark, I was hoping to get away without achieving sync. If i can avoid cutting 3 teeth off each cam, that would be ideal as by opening the new factory crate engine, I'd void the warranty.

dougsgh, 2024-05-28:
Ok, issue resolved. I figured out that vvt wasn't happy without a valid coolant temperature.

I first rolled back to 23 firmware, that didn't work, once I added coolant temp sensor, things came to life, rolled forward to 24 release current firmware, and vvt1 and 2 outs are working in open loop, closed loop not working quite right due to my 4t tooth setup. It does log a fixed incorrect cam angle after a tooth log and I was able to get PID to try and chase it and put some pwm out.

Apologies for the newbie errors here!

Now for a crash course in C++ and decoder logic 🤣

h25r, 2024-05-28:
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

The crankshaft has 60 teeth with 2 missing, and the camshafts are half-moon.
Motor is m52tub25 dual vanos. both vanos have half-moon trigger

noisymime, 2024-05-29:
> I am a little confused however, the trigger setting I have is set to single tooth, am I missing something?

Sorry, I had mixed up to the 2 tunes in this issue and was looking at the one from @h25r!

Unfortunately I do think that a dedicated decoder pattern is going to be your only option. Do you have any timing diagrams for the pattern at all?

noisymime, 2024-05-29:
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

OK, spun this up to test today. What I can see in your log is that the VVT1 angle reading is exceeding your Max Cam angle setting of 42. This is what is putting the VV1 into an error state and turning off the output as a failsafe.

See what happens if you increase your Max Cam Angle setting up to 43 or 44. That should enable the output and clear the error that is showing.
On the bench here I took your tune, upped the Max Cam Angle to 50 and am getting a VVT output as expected.

noisymime, 2024-05-29:
@h25r Actually, I've also just pushed up 1 more small change that might help in your specific case. Try the master firmware again from SpeedyLoader and see if you get any difference.

dougsgh, 2024-05-29:
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

Thank-you, that would be amazing!

I mapped out the pattern in excel, cam in locked position. The cam tooth aligns 8 teeth after the gap in the crank trigger for both cams. (vvt1&2) (This can be seen in the scope trace picture above).

Unfortunately no way to get sync without the inlet cam's, however I have no plans in running fuel or spark. I only plan for this to be a VVT controller.

[VK56TriggerExhaust.xlsx](https://github.com/noisymime/speeduino/files/15478837/VK56TriggerExhaust.xlsx)

h25r, 2024-05-29:
> @h25r Actually, I've also just pushed up 1 more small change that might help in your specific case if you're getting 0 for VVT readings. Try the master firmware again from SpeedyLoader and see if you get any difference.

working perfect now with the change you suggested. Thank you very much, i will sent couple beers to u!

dougsgh, 2024-05-31:
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

I was hoping this was just a tunerstudio display issue, but i confirmed that I do not have vvt1 output until i plug in ts and hit tooth log. Those PID settings are doing great though!

noisymime, 2024-05-31:
@dougsgh Which decoder are you using now, the missing tooth one? If so, try the master firmware and see if it's any change.

Also.... I'm guessing the RPM figure is doubled? 🤣

dougsgh, 2024-06-01:
@noisymime Winning! Thank-you, master works! 2 stroke 5.6l v8, revving to 12000rpm would be a beast 🤣. Running missing tooth, and single tooth cam. No change to the stock 36-2-2 crank or 4t cams. Those pids have the cam angle following incredibly well. Bit more street tuning and then some dyno time. 👍

Closed 2024-05-26.

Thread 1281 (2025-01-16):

Idle valve settings - Run before start option - Strange behaviour

Nawakland, 2025-01-16:
Evening,
Trying to smooth cranking and starting phase of my engine, I'm facing some strange behaviors with Idle valve settings.
There is a "run before start" option in idle valve settings and according to tips : should open idle valve before cranking to help starting to flow more air.
But when I tick this option and power the ECU (engine not running) my fuel pump doesn't stop, idle valve move back and forth and injectors don't stop priming.
I think there is something I'm doing wrong, can you provide me some clue ?

Speeduino version February 2024 Fix Pack 2 (FP2)
PWM open loop, 160Hz
3 wires idle valve

Nawakland, 2025-01-16:
EDIT : Missing hardware info
Arduino MEGA official
Board wtmtronics UA4C Version vC5 White Fang
Speeduino version February 2024 Fix Pack 2 (FP2)

Nawakland, 2025-02-11:
Wrong close.

Closed 2025-02-11.

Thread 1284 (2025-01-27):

Irradic Flex Fuel readings on Teensy 4.1

RempageR1, 2025-01-27:
I was testing a generic Flex-Fuel sensor (#13577429) on the Teensy 4.1 using E5 petrol but got very irradic readings. To start, I connected my scope to the pin directly on the Teensy:

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

And that looked clean enough :).

Looking at the code, the FlexFuel sensor input gets an interrupt attached that triggers plexPulse() on change. If the pin then reads true, flexCounter is increased by 1. After a second, the pulses are counted and the frequency is known. However when adding some simple debug code, the READ_FLEX() dit not return true, false, true, false etc. but true, true, false, true, false, false etc. It seems the Teensy really needs a VR conditioner or so to read such values. So I added a check to flexPulse(void) to check if the last value was different. That got it 99% working, but still some irradic spikes.

This was caused by some pulses being so quick they could never be correct, like the second pulse after 20 microseconds. To fix this, I only allowed pulses that had a delta > 1ms. So if a sensor stays below 1000hz, it should be fine :).

The final code looks like this which outputs 55hz, exactly matching my E5 petrol:

void flexPulse(void)
{
  if(READ_FLEX() == true)
  {
    if (lastFlex == false){
      if ((micros() - flexStartTime) > 1000){
        uint16_t tempPW = clamp(micros() - flexStartTime, 0UL, (unsigned long)UINT16_MAX); //Calculate the pulse width
        flexPulseWidth = LOW_PASS_FILTER(tempPW, configPage4.FILTER_FLEX, flexPulseWidth);
        ++flexCounter;
      }
      lastFlex = true;
    }
  }
  else
  {
    if (lastFlex == true){
      flexStartTime = micros(); //Start pulse width measurement.
      lastFlex = false;
    }
  }
}

I think this will also help other users with the Teensy. If needed, I can clean up the code a bit and create a pull request. Just let me know. Thank you.

noisymime, 2025-01-27:
Can you try adding this code into the `setTriggerHysteresis()` function within the `board_teensy41.cpp` file and see if it makes any difference?

```
//Flex trigger
p = digital_pin_to_info_PGM + pinFlex;
*(p->reg + 1) &= ~(p->mask); // TODO: atomic
*(p->pad) = padConfig;
*(p->mux) = 5 | 0x10;
```

RempageR1, 2025-01-29:
Hi noisymime,

I`ve tested that and indeed that fixes the problem and is also a much nicer solution :)

Thank you!

noisymime, 2025-01-29:
@RempageR1 Thanks for confirming! A fix has been pushed for this now that also includes the VSS and knock external interrupt pins.

Closed 2025-01-29.

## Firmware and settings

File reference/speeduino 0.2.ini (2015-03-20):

;-------------------------------------------------------------------------------

[MegaTune]
   MTversion      = 2.25 ; MegaTune itself; needs to match exec version.

   queryCommand   = "Q"
   signature      = 20

;-------------------------------------------------------------------------------

[Constants]

   ;----------------------------------------------------------------------------
   ; Constants Definition
   ; --------------------
   ;
   ; Scalar Values
   ; -------------
   ; The scaling and translation values are used as follows:
   ;    msValue   = userValue / scale - translate
   ;    userValue = (msValue + translate) * scale
   ;
   ;
   ; Temperatures are fine, check out the Fielding IAC example (fastIdleT).
   ;
   ; Array Values
   ; ------------
   ; Arrays are specified just like scalars, except that they have a "shape"
   ; entry in the fourth parameter.  The shape allows you to define lists or
   ; tables, for example [8] defines a list with eight values and [2x4] defines
   ; a table with eight values (two rows and four columns).  Tables may be
   ; stored in either "X-" or "Y-order."  X-order means that memory is layed
   ; out like.
   ;
   ;     [x1,y1] [x2,y1]...[xn,y1] [x1,y2]...
   ;
   ; Y-order would be
   ;
   ;     [x1,y1] [x1,y2]...[x1,yn] [x2,y1]...
   ;
   ; To use the TableEditor, you must define two lists and a table, and
   ; the lengths of the lists must correspond to the shape of the table.
   ;
   ; Bit Fields
   ; ----------
   ; Bits are numbered 0-7, the rightmost being bit zero.  The basic
   ; data word that stores bit fields must be unsigned.
   ;
   ; You need NOT supply the correct number of labels matching the
   ; number of bits you've specified (one bit requires 2 values, two
   ; bits requires 4 values and so on).  If you neglect to supply enough
   ; labels, they will be synthesized using the sequence "1", "2" and so
   ; on based upon their position in the sequence (the cltType and matType
   ; will end up with identical lists).
   ;
   ; If you specify a label as "INVALID" (all upper case), then it will
   ; not be displayed in the combo box, so you can leave out values that
   ; make no sense.
   ;
   ;----------------------------------------------------------------------------

   endianness          = big
   nPages              = 3
   burnCommand         = "B"
   ; pageSize            = 125
   pageSize            = 128,       128,    128
   pageActivationDelay = 10
;  pageActivate        = ""
   pageActivate        = "P\001",   "P\002", "P\003"
   pageReadCommand     = "V",       "V",     "V"
   pageValueWrite      = "W%o%v",   "W%o%v", "W%o%v"
;  pageChunkWrite      = ""      ; No chunk write for standard MS
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

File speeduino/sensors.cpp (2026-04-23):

/*
Speeduino - Simple engine management for the Arduino Mega 2560 platform
Copyright (C) Josh Stewart
A full copy of the license may be found in the projects root directory
*/
/** @file
 * Read sensors with appropriate timing / scheduling.
 */
#include <SimplyAtomic.h>
#include "sensors.h"
#include "crankMaths.h"
#include "globals.h"
#include "maths.h"
#include "storage.h"
#include "comms.h"
#include "idle.h"
#include "corrections.h"
#include "pages.h"
#include "decoders.h"
#include "auxiliaries.h"
#include "utilities.h"
#include "unit_testing.h"
#include "sensors_map_structs.h"

bool auxIsEnabled;

static volatile uint32_t vssTimes[VSS_SAMPLES] = {0};
static volatile uint8_t vssIndex = 0U;

volatile uint8_t flexCounter = 0U;
static volatile uint32_t flexStartTime = 0UL;
volatile uint32_t flexPulseWidth = 0U;

static map_algorithm_t mapAlgorithmState;

/**
 * @brief A specialist function to map a value in the range [0, 1023] (I.e. 10-bit) to a different range.
 * 
 * Mostly used for analog input voltage level to real world value conversions.
 * 
 * @details
 * analogRead returns a number in the range [0, 1023], representing the pin input 
 * voltage from min to max (typically 0V - 5V)
 * We need to convert that value to the real world value the sensor is reading (pressure, temperature etc.)
 * If:
 *    * rangeMin is the real world value when the sensor is reading 0V
 *    * rangeMax is the real world measurement when the sensor is reading 5V
 *    * There is a linear relationship between voltage output and the real world value.
 * 
 * then this function will return the real world measurement (kPa, °C etc)
 * 
 * @param value Value to map (should be in range [0, 1023])
 * @param rangeMin Minimum of the output range
 * @param rangeMax Maximum of the output range
 * @return int16_t 
 */
TESTABLE_INLINE_STATIC int16_t fastMap10Bit(uint16_t value, int16_t rangeMin, int16_t rangeMax) 
{
  uint16_t range = rangeMax-rangeMin; // Must be positive (assuming rangeMax>=rangeMin)
  uint16_t fromStartOfRange = (uint16_t)rshift<10>((uint32_t)value * range);
  return rangeMin + (int16_t)fromStartOfRange;
}

//
static inline uint16_t readAnalogPin(uint8_t pin) 
{
  // Why do we read twice? Who knows.....
  analogRead(pin);
  // According to the docs, analogRead result should be in range 0-1023
  // Clip the result to zero minimum to prevent rollover just in case
  int tmp = analogRead(pin);
  // max is a macro on some platforms - DO NOT place the call to analogRead as an inline parameter:
  // (you might end up calling it twice)
  return max(0, tmp);
}


#if defined(ANALOG_ISR)
static volatile uint16_t AnChannel[16];
static inline uint16_t readAnalogSensor(uint8_t pin) {
  return AnChannel[pin-A0];
}
static inline uint16_t readMAPSensor(uint8_t pin) {
#if defined(ANALOG_ISR_MAP)
  return AnChannel[pin-A0];
#else
  return readAnalogPin(pin);
#endif
}
#define ADMUX_DEFAULT_CONFIG  0x40 //AVCC reference, ADC0 input, right adjusted, ADC enabled

ISR(ADC_vect)
{
  byte nChannel = (ADMUX & 0x07);

  byte result_low = ADCL;
  byte result_high = ADCH;

  #if defined(__AVR_ATmega1281__) || defined(__AVR_ATmega2561__)
    if (nChannel == 7U) { ADMUX = 0x40; }
  #elif defined(__AVR_ATmega1280__) || defined(__AVR_ATmega2560__)
    if( BIT_CHECK(ADCSRB, MUX5) ) { nChannel += 8; }  //8 to 15
    if(nChannel == 15U)
    {
      ADMUX = ADMUX_DEFAULT_CONFIG; //channel 0
      ADCSRB = 0x00; //clear MUX5 bit

      BIT_CLEAR(ADCSRA,ADIE); //Disable interrupt as we're at the end of a full ADC cycle. This will be re-enabled in the main loop
    }
    else if (nChannel == 7U) //channel 7
    {
      ADMUX = ADMUX_DEFAULT_CONFIG;
      ADCSRB = 0x08; //Set MUX5 bit
    }
  #endif
    else { ADMUX++; }

  //ADMUX always appears to be one ahead of the actual channel value that is in ADCL/ADCH. Subtract 1 from it to get the correct channel number
  if(nChannel == 0U) { nChannel = 16;} 
  AnChannel[nChannel-1] = (result_high << 8) | result_low;
}
#else
static inline uint16_t readAnalogSensor(uint8_t pin) {
  return readAnalogPin(pin);
}
static inline uint16_t readMAPSensor(uint8_t pin) {
  return readAnalogPin(pin);
}
#endif

/** Init all ADC conversions by setting resolutions, etc.
 */
void initialiseADC(void)
{
#if defined(__AVR_ATmega1280__) || defined(__AVR_ATmega1281__) || defined(__AVR_ATmega2560__) || defined(__AVR_ATmega2561__) //AVR chips use the ISR for this

  #if defined(ANALOG_ISR)
    noInterrupts(); //Interrupts should be turned off when playing with any of these registers

    ADCSRB = 0x00; //ADC Auto Trigger Source is in Free Running mode

    ADMUX = ADMUX_DEFAULT_CONFIG;  //Select AVCC as reference, ADC Right Adjust Result, Starting at channel 0

    //All of the below is the longhand version of: ADCSRA = 0xEE;
    #ifndef ADFR
      #define ADFR 5 //Looks like this is now defined. Retain this for compatibility with earlier versions of Arduino IDE that did not have this.
    #endif
    BIT_SET(ADCSRA,ADFR); //Set free running mode
    BIT_SET(ADCSRA,ADIE); //Set ADC interrupt enabled
    BIT_CLEAR(ADCSRA,ADIF); //Clear interrupt flag

    // Set ADC clock to 125KHz (Prescaler = 128)
    BIT_SET(ADCSRA,ADPS2);
    BIT_SET(ADCSRA,ADPS1);
    BIT_SET(ADCSRA,ADPS0);

    BIT_SET(ADCSRA,ADEN); //Enable ADC

    interrupts();
    BIT_SET(ADCSRA,ADSC); //Start conversion

  #else
    //This sets the ADC (Analog to Digital Converter) to run at 1Mhz, greatly reducing analog read times (MAP/TPS) when using the standard analogRead() function
    //1Mhz is the fastest speed permitted by the CPU without affecting accuracy
    //Please see chapter 11 of 'Practical Arduino' (books.google.com.au/books?id=HsTxON1L6D4C&printsec=frontcover#v=onepage&q&f=false) for more detail
     BIT_SET(ADCSRA,ADPS2);
     BIT_CLEAR(ADCSRA,ADPS1);
     BIT_CLEAR(ADCSRA,ADPS0);
  #endif
#elif defined(ARDUINO_ARCH_STM32) //STM32GENERIC core and ST STM32duino core, change analog read to 12 bit
  analogReadResolution(10); //use 10bits for analog reading on STM32 boards
#endif
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

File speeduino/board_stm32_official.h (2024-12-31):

#ifndef STM32OFFICIAL_H
#define STM32OFFICIAL_H
#include <Arduino.h>
#if defined(STM32_CORE_VERSION_MAJOR)
#include <HardwareTimer.h>
#include <HardwareSerial.h>
#include "STM32RTC.h"
#include <SPI.h>

#ifndef PLATFORMIO
  #ifndef USBCON
    #error "USBCON must be defined in boards.txt"
  #endif
  #ifndef USBD_USE_CDC
    #error "USBD_USE_CDC must be defined in boards.txt"
  #endif
#endif

#if defined(STM32F1)
  #include "stm32f1xx_ll_tim.h"
#elif defined(STM32F3)
  #include "stm32f3xx_ll_tim.h"
#elif defined(STM32F4)
  #include "stm32f4xx_ll_tim.h"
  #if defined(STM32F407xx) && !defined(HAL_CAN_MODULE_ENABLED)
    #warning "CAN module is not enabled. Internal CAN will NOT be available"
  #endif
#else /*Default should be STM32F4*/
  #include "stm32f4xx_ll_tim.h"
#endif
/*
***********************************************************************************************************
* General
*/
#define PORT_TYPE uint32_t
#define PINMASK_TYPE uint32_t
#define COMPARE_TYPE uint16_t
#define COUNTER_TYPE uint16_t
#define SERIAL_BUFFER_SIZE 517 //Size of the serial buffer used by new comms protocol. For SD transfers this must be at least 512 + 1 (flag) + 4 (sector)
#define FPU_MAX_SIZE 32 //Size of the FPU buffer. 0 means no FPU.
#define micros_safe() micros() //timer5 method is not used on anything but AVR, the micros_safe() macro is simply an alias for the normal micros()
#define TIMER_RESOLUTION 4

//Select one for EEPROM,the default is EEPROM emulation on internal flash.
//#define SRAM_AS_EEPROM /*Use 4K battery backed SRAM, requires a 3V continuous source (like battery) connected to Vbat pin */
//#define USE_SPI_EEPROM PB0 /*Use M25Qxx SPI flash on BlackF407VE*/
//#define FRAM_AS_EEPROM /*Use FRAM like FM25xxx, MB85RSxxx or any SPI compatible */

#ifndef word
  #define word(h, l) ((h << 8) | l) //word() function not defined for this platform in the main library
#endif  
  
#if defined(ARDUINO_BLUEPILL_F103C8) || defined(ARDUINO_BLUEPILL_F103CB) \
  || defined(ARDUINO_BLACKPILL_F401CC) || defined(ARDUINO_BLACKPILL_F411CE)
  //STM32 Pill boards
  #ifndef NUM_DIGITAL_PINS
    #define NUM_DIGITAL_PINS 35
  #endif
  #ifndef LED_BUILTIN
    #define LED_BUILTIN PB1 //Maple Mini
  #endif
#elif defined(STM32F407xx)
  #ifndef NUM_DIGITAL_PINS
    #define NUM_DIGITAL_PINS 75
  #endif
#endif

//Specific mode for Bluepill due to its small flash size. This disables a number of strings from being compiled into the flash
#if defined(MCU_STM32F103C8) || defined(MCU_STM32F103CB)
  #define SMALL_FLASH_MODE
#endif

#define BOARD_MAX_DIGITAL_PINS NUM_DIGITAL_PINS
#define BOARD_MAX_IO_PINS NUM_DIGITAL_PINS
#if __GNUC__ < 7 //Already included on GCC 7
extern "C" char* sbrk(int incr); //Used to freeRam
#endif
#ifndef digitalPinToInterrupt
inline uint32_t  digitalPinToInterrupt(uint32_t Interrupt_pin) { return Interrupt_pin; } //This isn't included in the stm32duino libs (yet)
#endif

#if defined(USER_BTN) 
  #define EEPROM_RESET_PIN USER_BTN //onboard key0 for black STM32F407 boards and blackpills, keep pressed during boot to reset eeprom
#endif

#if defined(STM32F407xx)
  //Comment out this to disable SD logging for STM32 if needed. Currently SD logging for STM32 is experimental feature for F407.
  #define SD_LOGGING
#endif

#if defined(SD_LOGGING)
  #define RTC_ENABLED
  //SD logging with STM32 uses SD card in SPI mode, because used SD library doesn't support SDIO implementation. By default SPI3 is used that uses same pins as SDIO also, but in different order.
  extern SPIClass SD_SPI; //SPI3_MOSI, SPI3_MISO, SPI3_SCK
  #define SD_CONFIG SdSpiConfig(SD_CS_PIN, DEDICATED_SPI, SD_SCK_MHZ(50), &SD_SPI)
  //Alternatively same SPI bus can be used as there is for SPI flash. But this is not recommended due to slower speed and other possible problems.
  //#define SD_CONFIG SdSpiConfig(SD_CS_PIN, SHARED_SPI, SD_SCK_MHZ(50), &SPI_for_flash)
#endif
#define USE_SERIAL3

//When building for Black board Serial1 is instantiated,building generic STM32F4x7 has serial2 and serial 1 must be done here
#if SERIAL_UART_INSTANCE==2
HardwareSerial Serial1(PA10, PA9);
#endif

extern STM32RTC& rtc;

void initBoard();
uint16_t freeRam();
void doSystemReset();
void jumpToBootloader();
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

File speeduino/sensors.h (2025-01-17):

#ifndef SENSORS_H
#define SENSORS_H

#include "globals.h"

// The following are alpha values for the ADC filters.
// Their values are from 0 to 240, with 0 being no filtering and 240 being maximum
#define ADCFILTER_TPS_DEFAULT   50U
#define ADCFILTER_CLT_DEFAULT  180U
#define ADCFILTER_IAT_DEFAULT  180U
#define ADCFILTER_O2_DEFAULT   128U
#define ADCFILTER_BAT_DEFAULT  128U
#define ADCFILTER_MAP_DEFAULT   20U //This is only used on Instantaneous MAP readings and is intentionally very weak to allow for faster response
#define ADCFILTER_BARO_DEFAULT  64U

#define ADCFILTER_PSI_DEFAULT  150U //not currently configurable at runtime, used for misc pressure sensors, oil, fuel, etc.

#define FILTER_FLEX_DEFAULT     75U

#define VSS_GEAR_HYSTERESIS 10U
#define VSS_SAMPLES         4U //Must be a power of 2 and smaller than 255

#define TPS_READ_FREQUENCY  30 //ONLY VALID VALUES ARE 15 or 30!!!

extern volatile byte flexCounter;
extern volatile uint32_t flexPulseWidth;

#if defined(CORE_AVR)
  #define READ_FLEX() ((*flex_pin_port & flex_pin_mask) ? true : false)
#else
  #define READ_FLEX() digitalRead(pinFlex)
#endif

extern bool auxIsEnabled;

void initialiseADC(void);
void readTPS(bool useFilter=true); //Allows the option to override the use of the filter
void readO2_2(void);
void flexPulse(void);
void knockPulse(void);
uint32_t vssGetPulseGap(byte toothHistoryIndex);
void vssPulse(void);
uint16_t getSpeed(void);
byte getGear(void);
byte getFuelPressure(void);
byte getOilPressure(void);
uint16_t readAuxanalog(uint8_t analogPin);
uint16_t readAuxdigital(uint8_t digitalPin);
void readCLT(bool useFilter=true); //Allows the option to override the use of the filter
void readIAT(void);
void readO2(void);
void readBat(void);
void readBaro(void);

/** @brief Initialize the MAP calculation & Baro values */
void initialiseMAPBaro(void);
void resetMAPcycleAndEvent(void);

void readMAP(void);

uint8_t getAnalogKnock(void);

/** @brief Get the MAP change between the last 2 readings */
int16_t getMAPDelta(void);

/** @brief Get the time in µS between the last 2 MAP readings */
uint32_t getMAPDeltaTime(void);

#endif // SENSORS_H

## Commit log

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2018-08-17 Fix for crank speed being wrong on Basic Distrbutor, Miata9905 and Subaru 67 patterns
    [speeduino.ino]
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2018-09-13 Add some missing parts for staging on different cylinder counts. Needs further testing (See #162)
    [speeduino.ino]
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2018-09-23 improve ini selection robustness to prevent impossible selection according to mcu type etc. allow canbus options to be chosen that were not previously available
    [cancomms.ino, sensors.ino, speeduino.ino]
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2018-12-03 Rmove injector opening time from the req_fuel multiplication on staged injection (Fixes #173)
    [speeduino.ino]
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2018-12-29 fix various typo in ts ini fix selection offset for aux in pins remove 511 limit on analog
    [sensors.ino, speeduino.ino]
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2019-01-08 Provide support for changing the idle stepper direction through the use of an "inverted Y/N" setting. This is to avoid the need to change wiring if it turns out the stepper is working in the opposite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
    [idle.ino]
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2019-01-15 Correctly handle case where sequential ignition is combined with more than 2 squirts per cycle. Is a potential fix for #187
    [speeduino.ino]
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2019-01-21 Prevent the 'Include AFR' option from working prior to the sensor warming up
    [timers.ino]
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2019-02-14 Fix a bug where calibration routines could potentially overwrite the early memory areas in EEPROM
    [sensors.ino]
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2019-02-27 Changes to idle stepper control to prevent idleControl() and disableIdle() from competing against each other. Also target the cranking stepper position when the engine stops and after initial homing 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
    [idle.ino]
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2019-03-07 Fix for Teensy not compiling when number of channels was set to 8/8
    [scheduler.ino]
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2019-04-11 cold start features
    Changed ASE percentage and duration from one fixed value to coolant based ones. And also fixed priming pulsewidth to be coolant based.
    [init.ino]
2019-04-12 Fix CLT based priming
    There was error in calculation and also the coolant temp wasn't read at all, so I needed to add coolant temp reading too.
    [init.ino]
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2019-04-16 Add option on readCLT() to skip the filter on startup. See #220
    [sensors.h, sensors.ino]
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2019-08-20 Fix second revolution check for MAP minimum
    Second revolution is never picked up with MAP Sample Method Set to cycle minimum as the +1 on the second check is in the wrong place
    [sensors.ino]
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2019-09-02 Correctly handle case where an analog pin is used for the fuel2 switching input
    [speeduino.ino]
2019-09-04 Use the end function pointers in overdwell protection for WastedCOP. Fixes #229
    [timers.ino]
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2019-10-01 Separate out stepper homing steps from maximum number of steps (#257)
    * Provide support for changing the idle stepper direction through the use
    of an "inverted Y/N" setting. This is to avoid the need to change wiring
    if it turns out the stepper is working in the opposite direction to what
    is expected.
    * Add a new setting maximum number of stepper motor steps, so that homing can be done more reliably.
    [idle.ino]
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2019-10-15 Only allow the 'Include AFR' option to run of the AFR warmup time has elapsed. Fixes #261
    [speeduino.ino]
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2019-10-22 Fix for potential underflow in staging code when DFCO enabled. Fixes #267
    [speeduino.ino]
2019-10-22 Fix MISRA violations (#268)
    * improve misra checking
    * fix 1600 misra violations
    * fix mistyped pointer
    * misra script was not filtering duplicates
    [board_avr2560.h, board_teensy35.h, idle.ino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]
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2019-11-07 Clear injector interrupt flag. Prevents false pulse at low RPM with seq. Fixes #266
    [board_avr2560.h, scheduler.ino]
2019-11-08 Add idle ignition timing correction feature (#275)
    * Add idle advance and idle switch settings
    Add idle RPM target based ignition timing correction
    * Change few names to avoid confusion
    changed idle switch to closed throttle position sensor (CTPS) and moved CTPS settings under idle advance settings dialog for now
    [init.ino, sensors.ino]
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2020-01-13 fix for serial0 and serial3 errors (#301)
    * fix to serial0 and serial3 when offset is 0 uses wrong command
    * fix to serial0 and serial3 when offset is 0 uses wrong command
    * fix hex num
    [cancomms.ino]
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2020-01-21 Pin mapping for BMW PnP boards (#295)
    BMW PnP pin mapping to support 6cyl fully seqvential. Basically same as v0.4 pin mapping, but in addition there is correct pins for ign/inj 5-6.
    [init.ino]
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2020-01-24 Early 2020 STM32 fixes (#308)
    * Some Fixes to work
    * Fix BluePill
    * Remove libmaple defs
    * STM32 Timers rework
    * GCC9 Fix
    * BlackPill update
    * Disable FRAM as default for STM32
    * STM32 storage options for all cores
    [board_stm32_official.h, board_stm32_official.ino, init.ino]
2020-01-24 enable teensy canbus interface (#307)
    * add teensy canbus library
    teensy can read and write functions enabled
    * update to teensyduino 1.49
    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
    [cancomms.ino, init.ino, speeduino.ino]
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2020-02-03 BlackPill fixes (#317)
    * STM32 fixes 2
    * Update FRAM lib
    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
    [board_stm32_official.h]
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2020-02-03 Separate one schedule unit test per function (#315)
    * one test per function
    * add tests
    * use initialiseSchedulers in tests
    * remove generic tests for schedules
    * fix schedule accuracy tests
    * fix warning static function never defined
    * fix test_schedule not working
    [scheduler.ino]
2020-02-07 201911 firmware introduced battery correction for deadtime only. When selected, currentStatus.batCorrection value remains at 100 and is useless to log in Tunerstudio. (#287)
    Opentime only -correction stuff was in speeduino.ino and whole time correction was in corrections.ino, moved all more logically to same place.
    [speeduino.ino]
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2020-02-11 Secondary serial requests are sometimes ignored (#321)
    * Fix to secondary serial requests to ensure the whole request is received before we attempt to process it. This avoids the situation where serial requests would sometimes be ignored when they are a multi-byte requests (e.g. the 'r' command).
    * Minor formatting change.
    [cancomms.ino]
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2020-02-13 Remove check on the OL Stepper idle for max temp. Fixes #322
    [idle.ino]
2020-02-18 Try to fix #311 (#324)
    * Fix previos ADC 'fixed definitions'
    * Fix duplicated pins
    * Typo
    * Fix compilation error for BluePill
    * Fix timers Prescale
    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
    [board_stm32_official.h, board_stm32_official.ino, init.ino]
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2020-02-27 Branch 082019ma (#326)
    * part 1 prepare structure for obd can port works
    rename old can_command() to secondarySerial_command() for secondary serial and create new can_command for real CAN instruction decode.
    fix masking for teensy 3x and 4
    * set mega as default build
    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
    [board_teensy35.h, cancomms.ino, init.ino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]
2020-02-27 6&8 cyl sequential ignition (#323)
    * Required changes done
    Needs testing
    * Additions
    * 8cyl changes for mega 2560
    * Decoder fixes
    [globals.ino, init.ino, scheduler.ino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]
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2020-03-16 Added cranking enrich range (#335)
    * First commit
    Increases cranking enrichment range from 0..255% to 0..1275%, accuracy is reduced to 5% steps but this should be enough.
    Max allowable gammae increased from 511% to 1500%, overflow in PW-function prevented.
    * Last one missed the second overflow prevention (less bitshift)
    * Version needs to be increased in order to avoid performing value update routine on every startup
    * Less bitshift is required only on iCorrections
    [speeduino.ino]
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2020-03-24 [ASE] Transition time to disable (#342)
    * [ASE] Transition time to disable
    * Real time ASE
    * Fix last commit
    * Fix variables declaration
    [globals.ino, timers.ino]
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2020-04-01 6 and 8 cylinder sequential injection (#280)
    * 6 cyl sequential related cleanup
    * disable 6cyl seq fuel trim tables for now
    * add the over 2 squirts fix
    * Add 5 and 6 cylinder semi and full sequential
    * 5 cylinder changes
    * fix priming pulse when using paired or semi-sequential injection
    * add 5 cyl special case back
    * Add missing 8 cyl stuff
    * add missing PW8
    * allow to change inj4Ang with non sequential 5 cylinder
    * add missing helptext
    [board_avr2560.h, globals.ino, init.ino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]
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2020-04-07 STM32F407 fixes (#338)
    * Correct overflow for 32bit timers
    * fix pins PA0-PA5 on some f407 boards
    * Enable access to SRAM Backup domain at boot
    * Add missing callback functions
    * Change timer resolutions. Corrects idle/aux timer frequencies
    * 32 bit overflow only for STM32F4
    [board_stm32_official.h, board_stm32_official.ino, cancomms.ino]
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2020-04-17 Configurable CS pin flash chip (#345)
    * fix building with spi flash as config storage
    * Fixing build with spi flash as EEPROM. Changed some pin numbers to match the board i am designing and testing now.
    * Now cs pin for spi eeprom is settable by flag in build enviroment.
    * Update platformio.ini
    debug tool added as default
    * fix building with spi flash as config storage
    * Fixing build with spi flash as EEPROM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
    [SPIAsEEPROM.cpp, board_stm32_official.h, board_stm32_official.ino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]
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2020-05-06 Idle Steeper motor cracking in closed loop (#371)
    * Idle Steeper motor cracking in closed loop
    Adding to run position while starting the engine..
    * Update speeduino.ini
    [idle.ino]
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2020-05-19 Bug fix: Pointers to Idle pins/port must always be initialized. (#375)
    * pointers to Idle pins must always be initialized. This is good practice. But this also gave problems with internal flash as EEPROM on STM32 otherwise.
    * cleanup
    [idle.ino]
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2020-05-21 [PID] Increase parameters and output resolution (#377)
    Parameters are 0.03125% for kP and kI, 0.00981% for kD. Increased output 4 times to give enought room for kP.
    PID now ignore compute if input is zero to avoid overshoot, kI and kD part as well.
    Added idlePID.Initialize() to crank part to start PID from a working condition.
    Show idleLoad when cranking.
    Fix TS numbers, increase max value
    [idle.ino]
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2020-05-29 Fix recently added functions (#393)
    Changed aseTsnDelay name to aseTaperTime
    Added a default aseTaperTime to 0.1S
    aseTsnStart isn't needed, removed
    Added IAC_STEP_OL taper, big thanks to Ryan
    Default dfcoMinCLT is 0C, added calibration offset and increased it to 40C as described on updates.ino
    Changed bitRead to BIT_CHECK
    Fix dfcoStart wasn't been reseted if conditions was droped before elapsed time causing next DFCO activation right away
    Few cosmetical changes on ini
    Update commits counter
    [idle.ino]
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2020-06-29 Fix crash on higher IGN channel setups when using trigger fixed cranking timing
    [init.ino, speeduino.ino]
2020-07-02 STM32F407 32bit timer issue fix (new) (#374)
    * Fixed 32 bit timers again
    * Set the battery voltage to a default value when board starts. So before a sensible value is read this is 0. The dwell correction is creating the ignition spurious pulses direct after reset of the board. (When "flying start" the engine)
    [board_stm32_official.h, board_stm32_official.ino, scheduler.ino]
2020-07-02 BlackPill update (#406)
    * BlackPill fix
    * Fix for disable timers
    * Fix STM32GENERIC
    [SPIAsEEPROM.cpp, board_stm32_official.h, board_stm32_official.ino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]
2020-07-03 Pinout corrections for STM32F407VE (#407)
    Some more corrections to move battery voltage measurement from pin PC6 to PC5. Because PC6 is not analog input capable (black_STM32F407VE boards).
    [init.ino]
2020-07-05 [FP] Add injector delay for priming (#391)
    * [FP] Add injector delay for priming
    * Fix build
    * Add the startup TPS read back in to ensure proper flood clear check
    [globals.ino, init.ino, scheduler.ino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]
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2020-07-08 Vbatt reading overflow fixed. sensors.ino (#409)
    * Update sensors.ino
    Prevent vbatt reading form going negative due to the vatVoltCorrect and overflowing the uint variable.
    Variable changed to signed int and added check to correct if gone negative.
    Thought given that all filters using the temp variable shoud remain working.
    * Update sensors.ino
    [sensors.ino]
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2020-07-26 [VVT] PID work (#412)
    * [VVT] PID work
    Tested on a half moon CAM pattern as working, it should work on others too.
    Added option to reverse the PWM output
    * Fix typo
    * Add second VVT pwm on same timer
    All precious VVT variables was renamed to VVT1 and added VVT2 stuff.
    Tested with logic analyzer.
    * Define VVT2 for other boards
    Added vvt2Pin
    * Just update on first tooth
    [auxiliaries.ino, init.ino, logger.ino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]
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2020-07-27 07072020 obdp3 (#411)
    * last part of main obd2 canbus for teensy MCU
    * tested obd2 for teensy3.5
    * Only init CAN on Teensy with 3.5. Otherwise this will lockup on 4.1
    Co-authore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
    [cancomms.ino, init.ino, speeduino.ino]
2020-07-29 Add "Half sync" indicator (#370)
    * Half sync indicator for 3 different trigger patterns.
    Added half sync indicator which shows that there is only primary trigger present for missing tooth, dual wheel and miata 9905 trigger patterns
    * missing tooth required some adjusting
    * forgot to remove stm32 pin mapping. I have it in other PR
    * Leave only for missing tooth
    [init.ino, speeduino.ino]
2020-07-29 Fixed step value. (#390)
    * Iac automatic resolution
    Fix idle stepper, work direct with values < 255 and keep existing mode
    * Fixed Hysteresis for stepper
    0 value bug the counter.
    * Fix value
    Changed value to 255.
    * Ensure no overflow on iacMaxSteps
    [idle.ino]
2020-07-30 new pinout STM32F407 board V0.5.0 and 0.5.1 (#423)
    * new pinout STM32F407
    * Put the #if directive on the correct side of the case 60: line.
    [init.ino]
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2020-08-09 Update on eeprom emulation (#424)
    * Fix building for FRAM with globals.h setting
    On request of vitor boss. A lot has been changed around to make the selection of EEPROM emulation type from the globals.h (including FRAM selection)
    * Add support for EEPROM emulation on internal flash of STM32F7
    * Updates on SPI Flash EEPROM
    * Fix building for BACKUPSRAM as EEPROM.
    * Add put() and get() functions to the EEPROM emulation. This is needed for the latest terminstor and other calibrations routines
    [SPIAsEEPROM.cpp, board_stm32_official.h]
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2020-08-12 Programmable outputs (#396)
    * Programmable outputs
    * Prevent array overflow
    * Show fullStatus variables names on dialog
    * Further fixes
    * Update with master
    [globals.ino, init.ino, speeduino.ino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]
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2020-08-15 [PW Math] Introduce fixed MAP multiply (#347)
    * [PW Math] Introduce fixed MAP multiply
    * Compilation fix
    [speeduino.ino]
2020-08-17 Fix for negative pressure sensor readings (#438)
    If the pressure sensor readings are negative, this fix will set the value to zero in that case.
    [sensors.ino]
2020-08-18 Flex fuel sensor temperature and temperature correction (#413). Also closes #252
    * Fuel temperature correction
    * fix negative temperatures
    * typo fixed
    [globals.ino, init.ino, sensors.h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]
2020-08-18 Bug fix and small improvement for local aux input channels (#398)
    * Add config error indicator
    * Fixes and naming change
    * Fixes
    * Change to fix conflicting error bit flag in init
    * Updating IO flag setting
    [init.ino, sensors.ino]
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2020-11-15 Add Idle up output (#378)
    Implement functionality to allow a defined output pin to toggle (normal or inverted) based on the idle up input pin.
    [globals.ino, idle.ino, init.ino]
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2020-11-16 Temporary fix for Teensy CanBus ALT pins being set (#476)
    * Temporary fix for Teensy CanBus ALT pins being set and not possible use pins 29 30 for other stuff.
    * Add comment indicating why the setRX/TX calls are needed
    [init.ino]
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2020-12-01 STM32 CAN bus library addition (#482)
    * CAN-bus library for STM32
    This adds CAN-bus library for STM32. Mainly for STM32F4, but others can be added later.
    * CAN2 and F446 support added for STM32 CAN library
    Adds support for second can interface and F446 bit timings.
    * Fix STM32 CAN pin selection and STM32F1 support
    The previous way to select CAN pins wasn't actually working, so this fixes that problem and also the F1 support too.
    * Fix building for Mega/Teensy
    * Update cancomms.ino
    * Update speeduino.ino
    [STM32_CAN.cpp, board_stm32_official.h, cancomms.ino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]
2020-12-01 Closed loop idle improve (#481)
    * Squashed commit of the following:
    commit c73f316fa5bf8c929a8fef5736f4a40045ea992f
    Author: Tjeerd <tjeerdie@users.noreply.github.com>
    Date: Wed Nov 25 21:53:45 2020 +0100
    cleanup and fix merge issues
    commit 57f1e8c6c73bcfb699b18ac51a2ec646be822f55
    Merge: 04478ca 131673d
    Author: Tjeerd <tjeerdie@users.noreply.github.com>
    Date: Wed Nov 25 18:59:58 2020 +0100
    Merge branch 'Closedloop_idle_improvements' into ClosedLoopIdleImprovement
    commit 131673dc60417cbc773b0763d2f93e917c83325f
    Author: Tjeerd <tjeerdie@users.noreply.github.com>
    Date: Sun Nov 22 21:54:03 2020 +0100
    more fiddeling with idle control
    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
    [board_stm32_official.ino, idle.ino]
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2020-12-01 Fix BMW PnP board pin mapping (#460)
    * Fix BMW PnP board pin mapping
    Remove duplicate uses of pin 48. Also add default VSS and Baro pins.
    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
    [init.ino]
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2020-12-02 Changes to prevent board lockup with initial run. (EEPROM all 0xFF) (#463)
    [init.ino, speeduino.ino]
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2020-12-02 STM32 jump to DFU bootloader (#485)
    * STM32 jump to DFU
    This enable jumping to hardware bootloader with software command.
    Based on @iLeeeZi previous work.
    * lowercase functions fixes
    [TS_CommandButtonHandler.ino, board_avr2560.h, board_avr2560.ino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]
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2020-12-07 Fix building stm32 f401 (#489)
    * fix building for STM32F401CC and general macro cleanup
    * Now building for all generic STM32F4x7 boards in arduino IDE is ok.
    * buildflag cleanup
    [STM32_CAN.cpp, board_stm32_official.h, board_stm32_official.ino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]
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2021-01-20 STM32 CAN-bus library fixes. (#503)
    * STM32 CAN library fixes
    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
    [STM32_CAN.cpp, cancomms.ino]
2021-01-22 STM32 CAN library improvement: addition of TX mailboxes (#508)
    * TX mailbox addition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
    [STM32_CAN.cpp]
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2021-01-29 Pin definition for user board (#425)
    * Pin definition for the Juice Box board
    Ignition-only user board
    Formatting corrections.
    * Added JUICEBOX user board
    User board and pin mappings
    * Updated platformio.ini to reflect noisymime
    * Add platformio.ini to gitignore
    * Updated pin mappings
    Pin mappings updated. Serial 2 now working
    * Removed platformio.ini
    * Match noisymime version
    * Match noisymime version (2nd attempt)
    Match noisymime version to allow merge.
    * JuiceBox pin layout added back in
    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
    [init.ino]
2021-01-29 Tweek EEPROM write frequency to try and prevent disconnect when doing temp calibrations
    [speeduino.ino]
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2021-02-01 Fix pin 54 selection (#511)
    Fix pin 54 listing and renamed macros to better understanding
    [board_teensy35.h, board_teensy41.h, board_template.h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]
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2021-02-04 couple of signed overflow fixes (#519)
    * the TS_CMD_VSS_RATIO* id values overflow signed 16 bit int on avr
    switch to unsigned 16 bit value
    define TS_CMD_VSS_60KMH 39168 //0x99x00
    define TS_CMD_VSS_RATIO1 39169
    define TS_CMD_VSS_RATIO2 39170
    define TS_CMD_VSS_RATIO3 39171
    define TS_CMD_VSS_RATIO4 39172
    define TS_CMD_VSS_RATIO5 39173
    define TS_CMD_VSS_RATIO6 39174
    * make sure we don't overflow and accidentally set negative timing
    currentStatus.advance can only hold a signed 8 bit value
    * make sure we can't have a negative multiplier
    [TS_CommandButtonHandler.ino]
2021-02-11 Dwell map addition (#525)
    * Add dwell map
    * Add information about the dwell settings
    * Fix copy/paste error
    [globals.ino, init.ino, speeduino.ino]
2021-02-13 Add Ford ST170 Decoder (#530)
    This adds a decoder for the Ford ST170 engine.
    This setup uses a 36-1 primary and a unique 8-3 secondary trigger.
    The existing missing tooth deooder with fixed parameters is used as the primary to reduce duplication.
    [init.ino]
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2021-02-22 Added poll level cam trigger type for missing tooth decoder. (#450)
    * poll-level setting for speeduino.ini
    * Update globals.h
    * Simple poll level decoder
    * Changed the poll level check to happen at tooth #1. Not at missing tooth.
    * Set trigger edge automatically correct to work with closed loop VVT.
    * Changed to READ_SEC_TRIGGER() -macro
    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
    [init.ino]
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2021-03-22 Create better support for STM32F401 and STM32F411 blackpills (#548)
    * Create support for STM32F401 and STM32F411 blackpills
    * Small bug introduced now fixed.
    [board_stm32_official.h, init.ino]
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2021-04-15 STM32 fixes and tweaks (#553)
    * STM32 fixes and tweaks
    Removed generic STM32F103 options from PlatformIO
    Added optional serial compilations on PlatforIO
    Make sure all timers are stoped at boot
    Small speed improve at SPIasEEPROM
    Added timers usage table to board_stm32_official.h
    * Added base board
    [Arduino Mega Shield.sch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]
2021-04-21 Isolate table3D member access in comms.ino (#545)
    * fix!: fix ODR violations
    * refactor: move page specific code into a separate CPP file
    * refactor: page getter/setter share mapping logic
    Extract common page-to-entity mapping logic from
    getPageValue() & setPageValue() - place in map_page_offset_to_entity()
    and share.
    * performance: optimize CRC calc
    Calculate page CRC by iterating over entities & tables.
    * CRC table calculation - use table iterator
    * refactor: use iterators for sendPage()
    Re-implement sendPage() using page & table iterators
    Future proof & fast
    * refactor: sendPageASCII()
    Pull put shared code into functions.
    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
    [board_stm32_official.h, board_stm32_official.ino, board_teensy35.h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]
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2021-04-21 Fix build warnings (#558)
    * Flag unused parameters
    * Fix compile warnings: abuse of static inline
    Place functions in correct order & only forward
    declare when necessary
    * Suppress unused parameter warnings
    [SPIAsEEPROM.cpp, auxiliaries.ino, cancomms.ino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]
2021-04-21 Additional compiler warning fixes (#561)
    * Remove unnecessary and invalid forward declarations
    * Flag unused parameter
    [board_teensy35.h, board_teensy41.h, comms.cpp]
2021-04-21 VVT2 addition and closed loop VVT improvement (#551)
    * VVT2 and closed loop VVT improvement
    * Fix building for latest changes
    * Fix CRC error
    [auxiliaries.ino, comms.cpp, globals.ino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]
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2021-05-21 Fix CORE4 Spare In 1 (#584)
    Pin A13 is "Sparein1", allocating it to the second O2 sensor prevents it from working, an unused pin (A5) has now been allocated to O2_2
    [init.ino]
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2021-06-19 Fix boost cut (#595)
    Reset boost cut bit and fix map reading when in Map reading = envent average and boost cut engage.
    [sensors.ino]
2021-07-04 Fixes for Arduino_Core_STM32 V2.0 (#592)
    Fixes and added FRAM to the code
    Fixes for Teensy 4.1
    [Fram.cpp, board_stm32_official.h, board_stm32_official.ino]
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2021-07-08 Added values to CANcomms (#588)
    * added status values to CANcom
    I added the missing status value to CANcomms to be able to acces them via serial.
    * Revert "added status values to CANcom"
    This reverts commit 2d0abb9f366ebb3e505f325177d1f8eb6bcd6288.
    * added status values to CANcomms
    added values to CANcomms to be able to acces them via serial
    * corrected the number of values
    * fixed the packet size
    * change order and some values
    I removed some status and added some
    * comments and remove double
    remove some status that where there two times and added comments for status1, 2, 3, 4
    [cancomms.ino]
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

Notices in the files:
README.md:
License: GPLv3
